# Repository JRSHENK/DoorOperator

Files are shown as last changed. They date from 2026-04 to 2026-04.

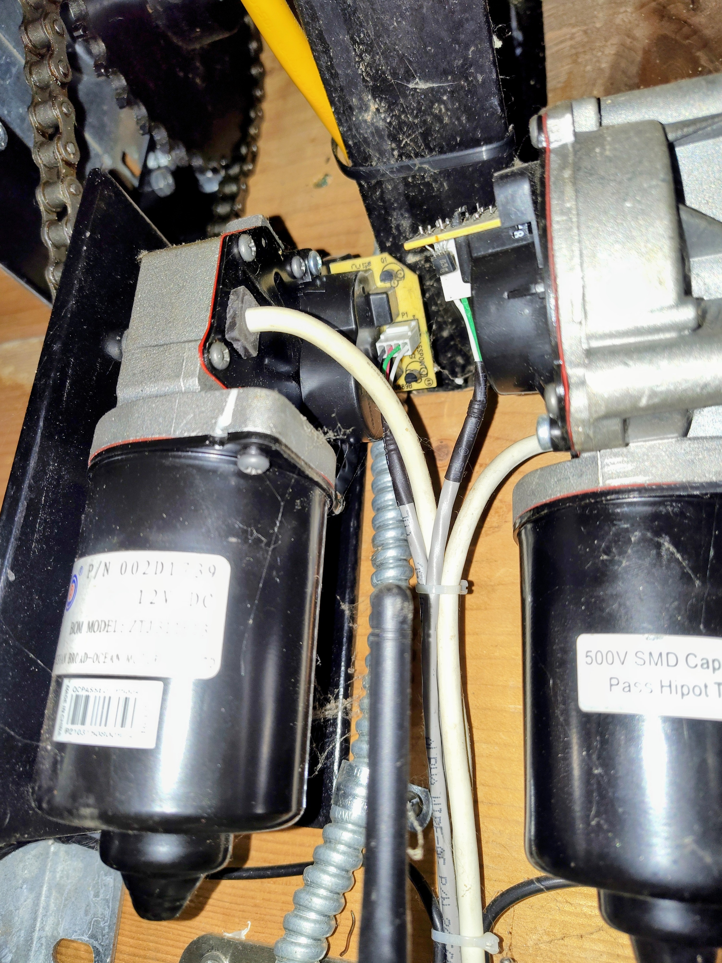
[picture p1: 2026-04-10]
photos/0314f007-4c58-49e5-93fa-2b8664fbc8d1~1.jpg

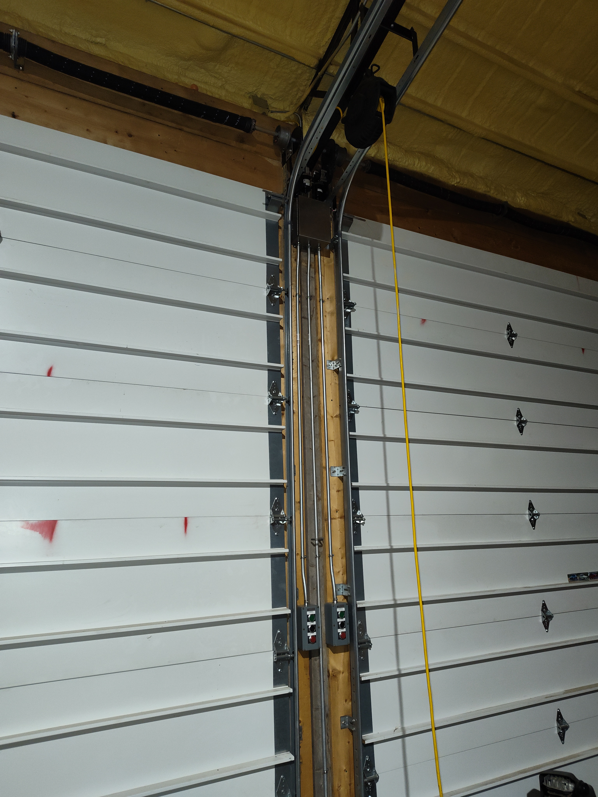
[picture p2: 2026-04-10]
photos/IMG_20260410_060428203.jpg

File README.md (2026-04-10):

This door operator uses an ESP32 to control 2 overhead door operator motors. The 2 Liftmaster 41D749 DC replacement motors are each driven by a BTS7960B H-bridge module (BT-2). The entire system is powered using (8) 18650 batteries I recovered from damage power tool battery packs that get trickle charged by a 16VDC supply. I monitor the battery voltage and motor currents using an INA219 module on each motor. The current is monitored while the door is moving and stops the motor if the current is more than expected. An optical beam is used to detect obstructions and stop the door. The position of the door is tracked using the optical shaft encoder built into the Liftmaster motors I used. The ESP32 has build in hardware counters, which eliminate the need to use interrupts in the code. I also use a hall effect sensor as a limit switch in the fully closed position as a reference for the position encoder. It just sets the counter to zero when the door is closed. This eliminates any counter errors from accumulating over time and gives a zero reference when initially installing.

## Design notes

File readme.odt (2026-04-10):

System Overview:

This door operator uses an ESP32 to control 2 overhead door operator motors. The 2 Liftmaster 41D749 DC replacement motors are each driven by a BTS7960B H-bridge module (BT-2). The entire system is powered using (8) 18650 batteries I recovered from damage power tool battery packs that get trickle charged by a 16VDC supply. I monitor the battery voltage and motor currents using an INA219 module on each motor. The current is monitored while the door is moving and stops the motor if the current is more than expected. An optical beam is used to detect obstructions and stop the door. The position of the door is tracked using the optical shaft encoder built into the Liftmaster motors I used. The ESP32 has build in hardware counters, which eliminate the need to use interrupts in the code. I also use a hall effect sensor as a limit switch in the fully closed position as a reference for the position encoder. It just sets the counter to zero when the door is closed. This eliminates any counter errors from accumulating over time and gives a zero reference when initially installing.

Battery holder and BMS:

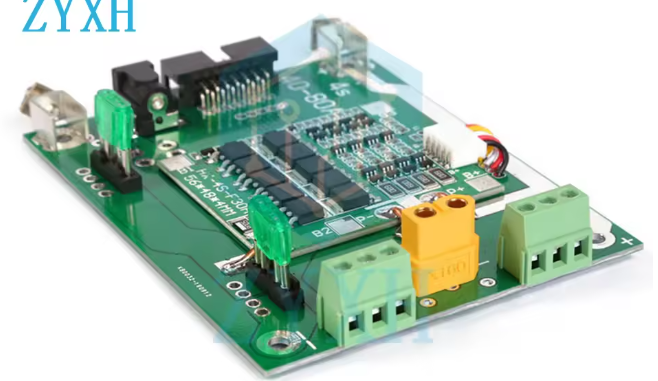
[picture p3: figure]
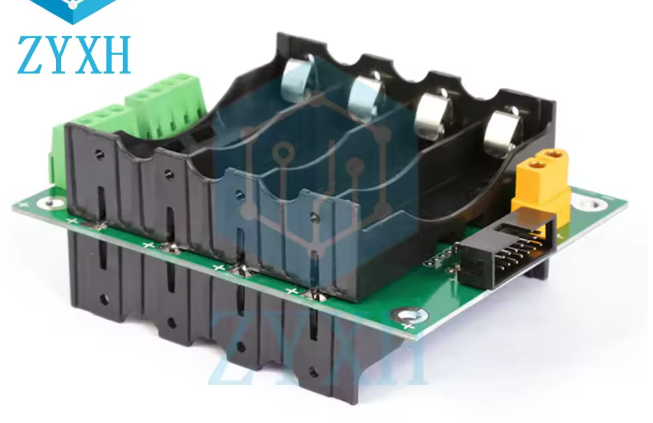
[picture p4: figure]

BTS7960B H-Bridge Module:

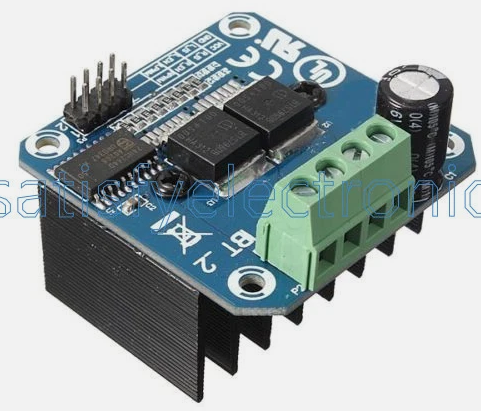
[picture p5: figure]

INA219 Modules:

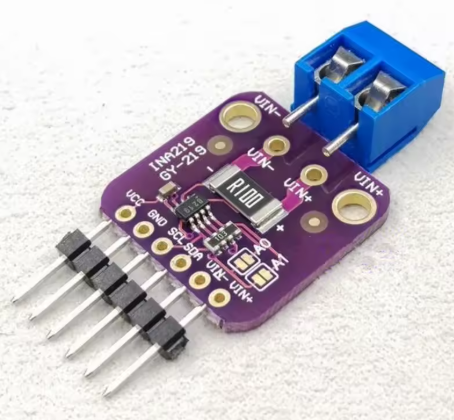
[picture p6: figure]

PCB:

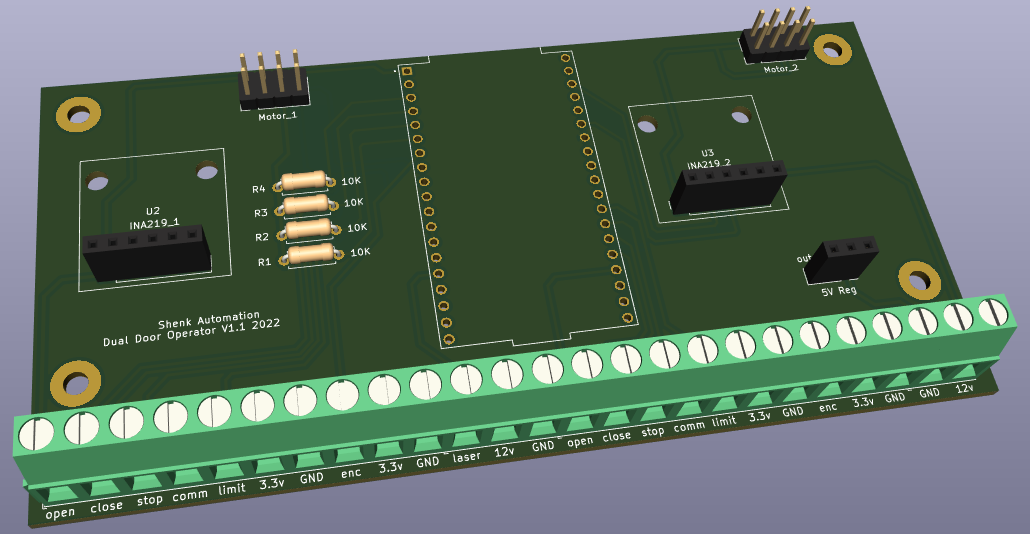
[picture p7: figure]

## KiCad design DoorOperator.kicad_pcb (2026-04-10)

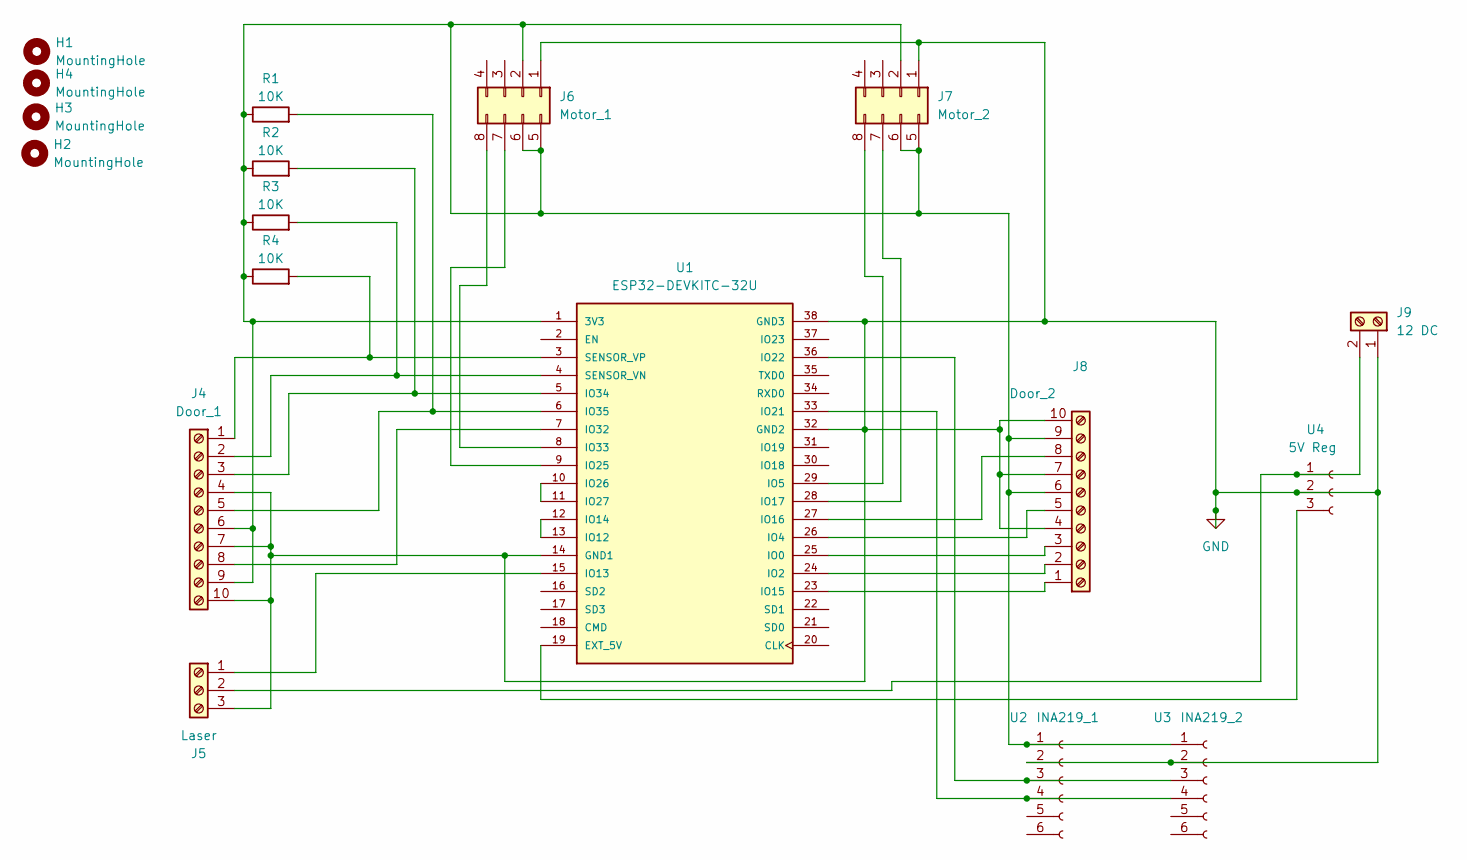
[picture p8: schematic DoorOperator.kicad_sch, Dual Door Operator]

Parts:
H1, H2, H3, H4: MountingHole; MountingHole_3.2mm_M3_Pad_TopBottom
J4: Door_1; TerminalBlock_Phoenix_MKDS-1,5-10_1x10_P5.00mm_Horizontal
J5: Laser; TerminalBlock_Phoenix_MKDS-1,5-3-5.08_1x03_P5.08mm_Horizont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
J6: Motor_1; PinHeader_2x04_P2.54mm_Vertical
J7: Motor_2; PinHeader_2x04_P2.54mm_Vertical
J8: Door_2; TerminalBlock_Phoenix_MKDS-1,5-10_1x10_P5.00mm_Horizontal
J9: 12 DC; TerminalBlock_Phoenix_MKDS-1,5-2_1x02_P5.00mm_Horizontal
R1, R2, R3, R4: 10K; R_Axial_DIN0207_L6.3mm_D2.5mm_P7.62mm_Horizontal
U1: ESP32-DEVKITC-32U; MODULE_ESP32-DEVKITC-32U; PARTREV N/A
U2: INA219_1; INA219_Module
U3: INA219_2; INA219_Module
U4: 5V Reg; PinSocket_1x03_P2.54mm_Vertical

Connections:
GND: J4.4, J4.7, J4.10, J5.3, J6.1, J7.1, J8.4, J8.7, J8.10, J9.1, U1.14 (GND1), U1.32 (GND2), U1.38 (GND3), U2.2, U3.2, U4.2
unnamed: J4.1, R4.2, U1.3 (SENSOR_VP)
unnamed: J4.2, R3.2, U1.4 (SENSOR_VN)
unnamed: J4.3, R2.2, U1.5 (IO34)
unnamed: J4.5, R1.2, U1.6 (IO35)
unnamed: J4.6, J4.9, J6.2, J6.5, J6.6, J7.2, J7.5, J7.6, J8.6, J8.9, R1.1, R2.1, R3.1, R4.1, U1.1 (3V3), U2.1, U3.1
unnamed: J4.8, U1.7 (IO32)
unnamed: J5.1, U1.15 (IO13)
unnamed: J5.2, J9.2, U4.1
unnamed: J6.7, U1.9 (IO25)
unnamed: J6.8, U1.8 (IO33)
unnamed: J7.7, U1.28 (IO17)
unnamed: J7.8, U1.29 (IO5)
unnamed: J8.1, U1.23 (IO15)
unnamed: J8.2, U1.24 (IO2)
unnamed: J8.3, U1.25 (IO0)
unnamed: J8.5, U1.26 (IO4)
unnamed: J8.8, U1.27 (IO16)
unnamed: U1.10 (IO26), U1.11 (IO27)
unnamed: U1.12 (IO14), U1.13 (IO12)
unnamed: U1.19 (EXT_5V), U4.3
unnamed: U1.33 (IO21), U2.4, U3.4
unnamed: U1.36 (IO22), U2.3, U3.3

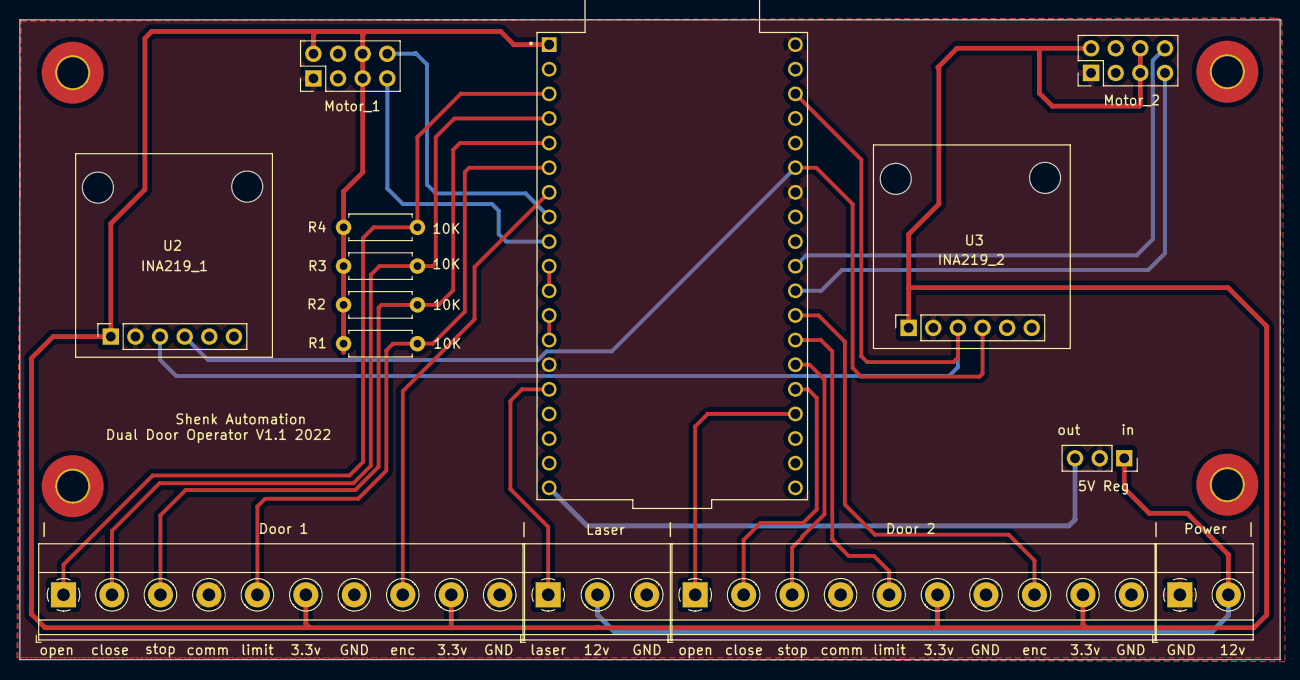
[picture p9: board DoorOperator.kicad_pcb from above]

Board: 2 copper layers, 130.0 x 66.0 mm, 18 parts (0 on the bottom side), 23 nets.

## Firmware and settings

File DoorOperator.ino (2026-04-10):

/***

   Overhead Door Opener V1.0.16.4 Octorber 2025
   For ESP32
   OTA Working
   changed to non-blocking
   MQTT reporting status & position
   Added encoder position removed approach limit switches
   Desired door position sent from MQTT in percent open
   Changed IO pins to make easier PCB trace layout
   Added INA219s & stop on over current
   Changed to be compatable with Arduino ESP32 V3.x.x 

*/

#define DOOR_OPERATOR_VERSION "1.0.16.4"

// libraries
#include <WiFi.h>
#include <Wire.h>
#include <PubSubClient.h>
#include <ESPmDNS.h>
#include <WiFiUdp.h>
#include <ArduinoOTA.h>
#include <ESP32Encoder.h>
#include <Adafruit_INA219.h>

//*************************  Set Debugging on or off **********************

// Comment the following line if not debuging
//#define __DEBUG__

#if defined(__DEBUG__)
#define DEBUG_begin(val) Serial.begin(val)
#define DEBUG_print(val) Serial.print(val)
#define DEBUG_println(val) Serial.println(val)
#else
#define DEBUG_begin(val)
#define DEBUG_print(val)
#define DEBUG_println(val)
#endif

#define sda 21  //Pin #33
#define scl 22  //Pin #36

// INA219 current and voltage sensors: to monitor battery panel & battery
Adafruit_INA219 ina219_door1(0x40);  // I2C address can be set to 0x40, 0x41, 0x44 or 0x45
Adafruit_INA219 ina219_door2(0x41);  // I2C address can be set to 0x40, 0x41, 0x44 or 0x45


//************************* Define Variables ******************************
ESP32Encoder encoder1;
ESP32Encoder encoder2;
char cPercentPosition1[10];
char cPercentPosition2[10];
String sCount1;
String sCount2;
int iCount1 = 0;
int iCount2 = 0;
int countPreset1 = 0;
int countPreset2 = 0;
int percentPosition1 = 0;
int percentPosition2 = 0;
int percentPreset1 = 0;
int percentPreset2 = 0;
#define fullCount 2100    // set this value to the number of counts needed for full door travel (My motor: 70 pulses/rev, 500 pulses/passpoint pulse)
#define slowDownCount 50  // set this value to how many counts before the end the door slows down at

#define direction_1 27    //Pin #11
#define openButton_1 36   //Pin #3
#define closeLimit_1 35   //Pin #6
#define closeButton_1 39  //Pin #4

//Reversed motor
//#define motorClose_1 25 //Pin #9
//#define motorOpen_1 33 //Pin #8
#define motorClose_1 33  //Pin #8
#define motorOpen_1 25   //Pin #9

#define stopButton_1 34  //Pin #5
#define openButton_2 15  //Pin #23
#define direction_2 12   //Pin #13
#define closeLimit_2 4   //Pin #26
#define closeButton_2 2  //Pin #24

//reversed motor
//int motorClose_2 5 //Pin #29
//int motorOpen_2 17 //Pin #28
#define motorClose_2 17  //Pin #28
#define motorOpen_2 5    //Pin #29

#define stopButton_2 0    //Pin #25
#define beam 13           //Pin #15
#define encoderCount1 32  //Pin #7
#define encoderDir1 26    //Pin #10
#define encoderCount2 16  //Pin #27
#define encoderDir2 14    //Pin #12

// Set these for desired door travel speeds 0-255
#define fast 255
#define slow 145

// Set these to a little longer than it takes for your door to open and close, so if something goes wrong the door operator does not get damaged (mS)
#define openTimeOut 32000
#define closeTimeOut 32000

// Set these to a little more than normal operating currents (mA)
#define openCurrentLimit 5100
#define closeCurrentLimit 5100

bool opening1 = false;
bool closing1 = false;
bool opening2 = false;
bool closing2 = false;
bool pubStat1 = false;
bool pubStat2 = false;
bool timeOut1 = false;
bool timeOut2 = false;
bool open1 = false;
bool open2 = false;
bool openSlow1 = false;
bool openSlow2 = false;
bool close1 = false;
bool close2 = false;
bool closeSlow1 = false;
bool closeSlow2 = false;
bool pubIP = true;
unsigned long runTime_1;
unsigned long runTime_2;
unsigned long startTime_1;
unsigned long startTime_2;
unsigned long endTime_1;
unsigned long endTime_2;
float busvoltage = 0;
float busvoltageNew = 0;
float door1_mA = 0;
float door2_mA = 0;

// pwm channel assinment
#define pwmOpen_1 0
#define pwmClose_1 1
#define pwmOpen_2 2
#define pwmClose_2 3

// pwm frequency assinment
#define frequency 1500
// pwm resolution assinment
#define resolution 8

//*************************  NETWORK INFO  ********************************
const char* ssid = "YourSSID";
const char* password = "YourPassword";
const char* hostName = "SouthBarnDoors";
const char* mqtt_server = "MQTT_Server_IP";
const char* mqtt_user = "MQTT_Username";
const char* mqtt_password = "MQTT_Password";
const char* mqtt_clent = "Overhead_Doors";

// Publish info about the status of door
const char* door1status = "Overhead_Doors/door1Status";
const char* door1position = "Overhead_Doors/door1Position";
const char* door2status = "Overhead_Doors/door2Status";
const char* door2position = "Overhead_Doors/door2Position";
const char* door1count = "Overhead_Doors/door1Count";
const char* door2count = "Overhead_Doors/door2Count";
const char* Vbattery = "Overhead_Doors/Vbattery";
const char* ip = "Overhead_Doors/ipAddress";

// Listen for incoming control messages
const char* doorControl = "Overhead_Doors/Control";
const char* door1SetValue = "Overhead_Doors/SetValue1";
const char* door2SetValue = "Overhead_Doors/SetValue2";
const char* HArefresh = "homeassistant/RefreshMQTT";

//*************************   MQTT String Setup ***************************

WiFiClient Overhead_Doors;
PubSubClient client(Overhead_Doors);
long lastMsg = 0;
char payload[50];
int value = 0;

//***************************  Setup WIFI  *********************************
void setup_wifi() {

  delay(10);
  // We start by connecting to a WiFi network
  DEBUG_println();
  DEBUG_print("Connecting to ");
  DEBUG_println(ssid);

  WiFi.begin(ssid, password);
  WiFi.setHostname(hostName);
  WiFi.setAutoReconnect(true);
  WiFi.persistent(true);


  DEBUG_println("");
  DEBUG_println("WiFi connected");
  DEBUG_println("IP address: ");
  DEBUG_println(WiFi.localIP());
}
//*********************  END WIFI SETUP  ************************************

void stopDoor_1();
void stopDoor_2();

//***********************  Reconnect to MQTT  ********************************
void reconnect() {
  // Loop until we're reconnected                         Remove this part
  //while (!client.connected()) {                         Remove this part
  //DEBUG_print("Attempting MQTT connection...");       Remove this part
  // Attempt to connect
  if (client.connect(mqtt_clent, mqtt_user, mqtt_password)) {
    DEBUG_println("connected");
    // Once connected, publish an announcement...
    //client.publish("outTopic", "hello world");
    client.subscribe(doorControl);
    client.subscribe(door1SetValue);
    client.subscribe(door2SetValue);
    client.subscribe(HArefresh);
  } else {
    DEBUG_print("failed, rc=");
    DEBUG_print(client.state());
    DEBUG_println(" try again in 5 seconds");
    // Wait 5 seconds before retrying                   Remove this part
    //delay(5000);                                      Remove this part
    //}                                                   Remove this part
  }
}

//***********   void callback listens for incoming mqtt messages  ***********
void callback(char* topic, byte* payload, unsigned int length) {
  DEBUG_print("Message arrived [");
  DEBUG_print(topic);
  DEBUG_print("] ");
  for (int i = 0; i < length; i++) {
    DEBUG_print((char)payload[i]);
  }
  DEBUG_println(" ");

  //************************************* MQTT Control *******************************************

  if (strcmp(topic, "homeassistant/RefreshMQTT") == 0) {
    pubStat1 = true;
    pubStat2 = true;
    pubIP = true;
  }

  if (strcmp(topic, "Overhead_Doors/SetValue1") == 0) {

    payload[length] = '\0';                     // Add a NULL to the end of the char* to make it a string.
    int percentPreset1 = atoi((char*)payload);  //Convert payload to int
    countPreset1 = ((fullCount) * (percentPreset1 * .01));

    if (countPreset1 > iCount1) {
      open1 = true;
    } else if (countPreset1 < iCount1) {
      close1 = true;
    }
  }

  if (strcmp(topic, "Overhead_Doors/SetValue2") == 0) {

    payload[length] = '\0';                     // Add a NULL to the end of the char* to make it a string.
    int percentPreset2 = atoi((char*)payload);  //Convert payload to int
    countPreset2 = ((fullCount) * (percentPreset2 * .01));


    if (countPreset2 > iCount2) {
      open2 = true;
    } else if (countPreset2 < iCount2) {
      close2 = true;
    }
  }

  // Stop door 1
  if ((char)payload[0] == 's' && (char)payload[1] == 't' && (char)payload[2] == 'o' && (char)payload[3] == 'p' && (char)payload[4] == '1') {
    stopDoor_1();
  }

  // Stop door 2
  if ((char)payload[0] == 's' && (char)payload[1] == 't' && (char)payload[2] == 'o' && (char)payload[3] == 'p' && (char)payload[4] == '2') {
    stopDoor_2();
  }

  //***************************************************************************
}


//****************************  BEGIN SETUP  **********************************
void setup() {

  Serial.begin(115200);
  while (!Serial) {
    ;  // wait for serial port to connect. Needed for native USB port only
  }

  Serial.print("Barn Door Opener ");
  Serial.println(DOOR_OPERATOR_VERSION);

  setup_wifi();
  client.setServer(mqtt_server, 1883);
  client.setCallback(callback);

  enableOTAfromIDE();
  ArduinoOTA.begin();

  Wire.begin(sda, scl);

  uint32_t currentFrequency;
  ina219_door1.begin();
  ina219_door2.begin();

  if (!ina219_door1.begin() || !ina219_door2.begin()) {
    DEBUG_println("Failed to find INA219 chip");
    while (1) {
      delay(10);
    }
  }

  DEBUG_println("Measuring voltage and current with INA219 ...");

  //Setup position encoders
  encoder1.attachSingleEdge(encoderCount1, encoderDir1);
  encoder2.attachSingleEdge(encoderCount2, encoderDir2);
  encoder1.setCount(0);
  encoder2.setCount(0);

  pinMode(direction_1, OUTPUT);
  pinMode(closeLimit_1, INPUT_PULLUP);
  pinMode(openButton_1, INPUT_PULLUP);
  pinMode(closeButton_1, INPUT_PULLUP);
  pinMode(stopButton_1, INPUT_PULLUP);

  pinMode(direction_2, OUTPUT);
  pinMode(closeLimit_2, INPUT_PULLUP);
  pinMode(openButton_2, INPUT_PULLUP);
  pinMode(closeButton_2, INPUT_PULLUP);
  pinMode(stopButton_2, INPUT_PULLUP);
  pinMode(beam, INPUT_PULLUP);

  pinMode(encoderCount1, INPUT_PULLUP);
  pinMode(encoderDir1, INPUT_PULLUP);
  pinMode(encoderCount2, INPUT_PULLUP);
  pinMode(encoderDir2, INPUT_PULLUP);

  pinMode(motorOpen_1, OUTPUT);
  pinMode(motorClose_1, OUTPUT);
  pinMode(motorOpen_2, OUTPUT);
  pinMode(motorClose_2, OUTPUT);

  ledcAttachChannel(motorOpen_1, frequency, resolution, pwmOpen_1);
  ledcAttachChannel(motorClose_1, frequency, resolution, pwmClose_1);
  ledcAttachChannel(motorOpen_2, frequency, resolution, pwmOpen_2);
  ledcAttachChannel(motorClose_2, frequency, resolution, pwmClose_2);

  ledcWriteChannel(pwmOpen_1, 0);
  ledcWriteChannel(pwmOpen_2, 0);
  ledcWriteChannel(pwmClose_1, 0);
  ledcWriteChannel(pwmClose_2, 0);
}
//*********************  END SETUP  ************************************


//*********************  BEGIN LOOP  ***********************************
void loop() {

  /*********      Check OTA Updates       ****************/
  ArduinoOTA.handle();

  if (!client.connected()) {
    reconnect();
  }
  client.loop();

  /**********************  Open Door 1  *******************************/
  if ((digitalRead(openButton_1) == LOW) && (iCount1 != fullCount)) {
    countPreset1 = fullCount;
    open1 = true;
  }

  if (iCount1 > (countPreset1 - slowDownCount) && (opening1 == true)) {
    openSlow1 = true;
  }

    //publish door position as door moves
  if ((open1 == true) || (openSlow1 == true)) {
    pubStat1 = true;
  }

  if ((closing1 == false) && (open1 == true) && (openSlow1 == false)) {
    ledcWriteChannel(pwmOpen_1, fast);
    client.publish(door1status, "Opening");
    open1 = false;
    opening1 = true;
    startTime_1 = millis();
    endTime_1 = startTime_1;
    timeOut1 == false;
  }

  if (opening1 == true) {
    endTime_1 = millis();
    sCount1 = String((int32_t)encoder1.getCount());
    iCount1 = sCount1.toInt();
    DEBUG_println(iCount1);

    door1_mA = ina219_door1.getCurrent_mA();

    if (door1_mA > openCurrentLimit) {
      stopDoor_1();
      client.publish(door1status, "trouble(I)");
      DEBUG_println("Door opening stopped over current!");
    }
  }

  if (openSlow1 == true && closing1 == false) {
    ledcWriteChannel(pwmOpen_1, slow);
    openSlow1 = false;
    client.publish(door1status, "Opening slow");
  }

  if ((digitalRead(stopButton_1) == LOW) || (digitalRead(beam) == LOW) || (countPreset1 <= iCount1) && (opening1 == true)) {
    stopDoor_1();
  }

  if (((endTime_1 - startTime_1) >= openTimeOut) && timeOut1 == false) {
    stopDoor_1();
    DEBUG_println("Door opening timed out!");
    client.publish(door1status, "trouble(T)");
    timeOut1 = true;
  }

  /**********************  Close Door 1  *******************************/
  if ((digitalRead(closeButton_1) == LOW) && (digitalRead(closeLimit_1) == HIGH)) {
    countPreset1 = 0;
    close1 = true;
  }

  if (iCount1 < (countPreset1 + slowDownCount) && (closing1 == true)) {
    closeSlow1 = true;
  }

    //publish door position as door moves
  if ((close1 == true) || (closeSlow1 == true)) {
    pubStat1 = true;
  }

  if ((opening1 == false) && (close1 == true) && (closeSlow1 == false)) {
    ledcWriteChannel(pwmClose_1, fast);
    digitalWrite(direction_1, HIGH);
    client.publish(door1status, "Closing");
    close1 = false;
    closing1 = true;
    startTime_1 = millis();
    endTime_1 = startTime_1;
    timeOut1 == false;
  }

  if (closing1 == true) {
    endTime_1 = millis();
    sCount1 = String((int32_t)encoder1.getCount());
    iCount1 = sCount1.toInt();
    DEBUG_println(iCount1);

    door1_mA = ina219_door1.getCurrent_mA();

    if (door1_mA > closeCurrentLimit) {
      stopDoor_1();
      client.publish(door1status, "trouble(I)");
      DEBUG_println("Door closing stopped, over current!");
    }
  }

  if (closeSlow1 == true && opening1 == false) {
    ledcWriteChannel(pwmClose_1, slow);
    client.publish(door1status, "Closing slow");
    closeSlow1 = false;
  }

  if (digitalRead(closeLimit_1) == LOW && (closing1 == true)) {
    encoder1.setCount(0);
    DEBUG_println("counter 1 reset");
    stopDoor_1();
  }

  if ((digitalRead(stopButton_1) == LOW) || (digitalRead(beam) == LOW) || ((countPreset1 >= iCount1) && (closing1 == true))) {
    stopDoor_1();
  }

  if (((endTime_1 - startTime_1) >= closeTimeOut) && timeOut1 == false) {
    stopDoor_1();
    DEBUG_println("Door closing timed out!");
    client.publish(door1status, "trouble(T)");
    timeOut1 = true;
  }

  /**********************  Open Door 2  *******************************/
  if ((digitalRead(openButton_2) == LOW) && (iCount2 != fullCount)) {
    countPreset2 = fullCount;
    open2 = true;
  }

  if (iCount2 > (countPreset2 - slowDownCount) && (opening2 == true)) {
    openSlow2 = true;
  }

   //publish door position as door moves
  if ((open2 == true) || (openSlow2 == true)) {
    pubStat2 = true;
  }

  if ((closing2 == false) && (open2 == true) && (openSlow2 == false)) {
    ledcWriteChannel(pwmOpen_2, fast);
    client.publish(door2status, "Opening");
    open2 = false;
    opening2 = true;
    startTime_2 = millis();
    endTime_2 = startTime_2;
    timeOut2 == false;
  }

  if (opening2 == true) {
    endTime_2 = millis();
    sCount2 = String((int32_t)encoder2.getCount());
    iCount2 = sCount2.toInt();
    DEBUG_println(iCount2);

    door2_mA = ina219_door2.getCurrent_mA();

    if (door2_mA > openCurrentLimit) {
      stopDoor_2();
      client.publish(door2status, "trouble(I)");
      DEBUG_println("Door opening stopped, over current!");
    }
  }

  if (openSlow2 == true && closing2 == false) {
    ledcWriteChannel(pwmOpen_2, slow);
    openSlow2 = false;
    client.publish(door2status, "Opening slow");
  }

  if ((digitalRead(stopButton_2) == LOW) || (digitalRead(beam) == LOW) || (countPreset2 <= iCount2) && (opening2 == true)) {
    stopDoor_2();
  }

  if (((endTime_2 - startTime_2) >= openTimeOut) && timeOut2 == false) {
    stopDoor_2();
    DEBUG_println("Door opening timed out!");
    client.publish(door2status, "trouble(T)");
    timeOut2 = true;
  }

  /**********************  Close Door 2  *******************************/
  if ((digitalRead(closeButton_2) == LOW) && (digitalRead(closeLimit_2) == HIGH)) {
    countPreset2 = 0;
    close2 = true;
  }

  if (iCount2 < (countPreset2 + slowDownCount) && (closing2 == true)) {
    closeSlow2 = true;
  }

       //publish door position as door moves
  if ((close2 == true) || (closeSlow2 == true)) {
    pubStat2 = true;
  }
  
  if ((opening2 == false) && (close2 == true) && (closeSlow2 == false)) {
    ledcWriteChannel(pwmClose_2, fast);
    digitalWrite(direction_2, HIGH);
    client.publish(door2status, "Closing");
    close2 = false;
    closing2 = true;
    startTime_2 = millis();
    endTime_2 = startTime_1;
    timeOut2 == false;
  }

  if (closing2 == true) {
    endTime_2 = millis();
    sCount2 = String((int32_t)encoder2.getCount());
    iCount2 = sCount2.toInt();
    DEBUG_println(iCount2);

    door2_mA = ina219_door2.getCurrent_mA();

    if (door2_mA > closeCurrentLimit) {
      stopDoor_2();
      client.publish(door2status, "trouble(I)");
      DEBUG_println("Door closing stopped, over current!");
    }
  }

  if (closeSlow2 == true && opening2 == false) {
    ledcWriteChannel(pwmClose_2, slow);
    client.publish(door2status, "Closing slow");
    closeSlow2 = false;
  }

  if (digitalRead(closeLimit_2) == LOW && (closing2 == true)) {
    encoder2.setCount(0);
    DEBUG_println("counter 2 reset");
    stopDoor_2();
  }

  if ((digitalRead(stopButton_2) == LOW) || (digitalRead(beam) == LOW) || ((countPreset2 >= iCount2) && (closing2 == true))) {
    stopDoor_2();
  }

  if (((endTime_2 - startTime_2) >= closeTimeOut) && timeOut2 == false) {
    stopDoor_2();
    DEBUG_println("Door closing timed out!");
    client.publish(door2status, "trouble(T)");
    timeOut2 = true;
  }

  /************************  Publish data  *********************************/
  if (pubIP == true) {

    String ipaddress = WiFi.localIP().toString();
    char ipchar[ipaddress.length() + 1];
    ipaddress.toCharArray(ipchar, ipaddress.length() + 1);
    client.publish(ip, ipchar);

    pubIP = false;
  }

  if (pubStat1 == true) {

    sCount1 = String((int32_t)encoder1.getCount());
    iCount1 = sCount1.toInt();
    percentPosition1 = (((iCount1 * 100) / fullCount));

    DEBUG_print("Door 1 percent open ");
    DEBUG_println(percentPosition1);
    DEBUG_print("icount1 ");
    DEBUG_println(iCount1);
    DEBUG_print("fullCount ");
    DEBUG_println(fullCount);


    dtostrf(percentPosition1, 3, 0, cPercentPosition1);
    client.publish(door1position, cPercentPosition1);
    DEBUG_println("published Door 1 Position");

    pubStat1 = false;
  }

  if (pubStat2 == true) {

    sCount2 = String((int32_t)encoder2.getCount());
    iCount2 = sCount2.toInt();
    percentPosition2 = (((iCount2 * 100) / fullCount));

    DEBUG_print(" Door 2 percent open ");
    DEBUG_println(percentPosition2);
    DEBUG_print("icount2 ");
    DEBUG_println(iCount2);
    DEBUG_print("fullCount ");
    DEBUG_println(fullCount);


    dtostrf(percentPosition2, 3, 0, cPercentPosition2);
    client.publish(door2position, cPercentPosition2);
    DEBUG_println("published Door 2 Position");

    pubStat2 = false;
  }

  long now = millis();
  if (now - lastMsg > 5000) {
    lastMsg = now;
    ++value;

    busvoltageNew = ina219_door1.getBusVoltage_V();
    if (busvoltage != busvoltageNew) {
      char battery_voltage_str[5];
      dtostrf(busvoltageNew, 2, 1, battery_voltage_str);
      client.publish(Vbattery, battery_voltage_str);
      busvoltage = busvoltageNew;
    }
  }
}
//***********************  END MAIN LOOP  ********************************

void stopDoor_1() {
  ledcWriteChannel(pwmOpen_1, 0);
  ledcWriteChannel(pwmClose_1, 0);
  digitalWrite(direction_1, LOW);
  opening1 = false;
  closing1 = false;
  open1 = false;
  close1 = false;
  openSlow1 = false;
  closeSlow1 = false;
  client.publish(door1status, "Stopped");
  pubStat1 = true;
}

void stopDoor_2() {
  ledcWriteChannel(pwmOpen_2, 0);
  ledcWriteChannel(pwmClose_2, 0);
  digitalWrite(direction_2, LOW);
  opening2 = false;
  closing2 = false;
  open2 = false;
  close2 = false;
  openSlow2 = false;
  closeSlow2 = false;
  client.publish(door2status, "Stopped");
  pubStat2 = true;
}
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
